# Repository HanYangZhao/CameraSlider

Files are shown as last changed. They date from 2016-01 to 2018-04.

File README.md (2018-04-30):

# Smartphone controlled camera slider using 3D Printed parts and Esp8266

This project started with me wanting to take timelapse photos and videos where the camera is sliding on a set of rails. Because my primary application was timelapse photos, I wanted something that was motorized and automated so that I don't have to manually adjust the slider and cause inconsistency the the photos. Additionally, I wanted to be able to control the rig with a smartphone. Commercial products costs over 500$ and none of them are wireless so I thought I'd make something for much cheaper using 3D printed parts and off the shelf components. The final total cost was under 100$. It is still an ongoing project.

# TODO: 

-iOS app

# Test Footage 

## Video

<a href="http://www.youtube.com/watch?feature=player_embedded&v=VQx5hUlplgQ
" target="_blank">IMAGE ALT TEXT HERE</a>

## Timelapse

<a href="http://www.youtube.com/watch?feature=player_embedded&v=VpbRqibYY6U
" target="_blank">IMAGE ALT TEXT HERE</a>

<a href="http://www.youtube.com/watch?feature=player_embedded&v=ssHNjMlmGzI
" target="_blank">IMAGE ALT TEXT HERE</a>

# Photos 

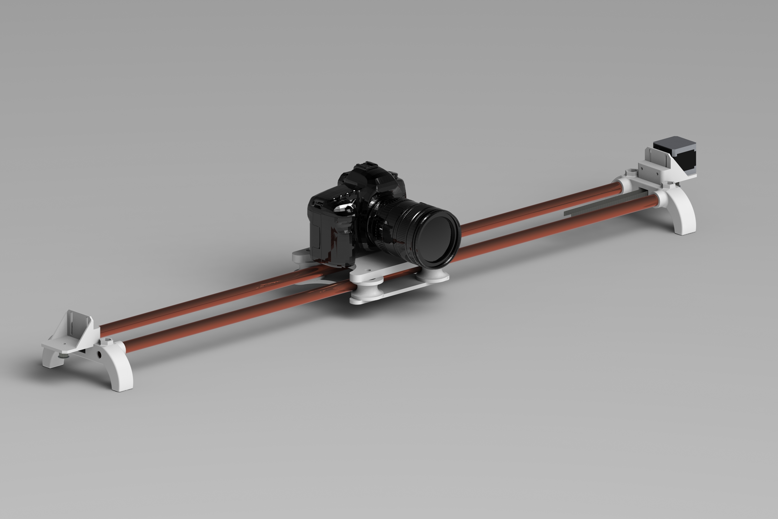
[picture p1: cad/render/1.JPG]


Designed using SolidWorks CAD

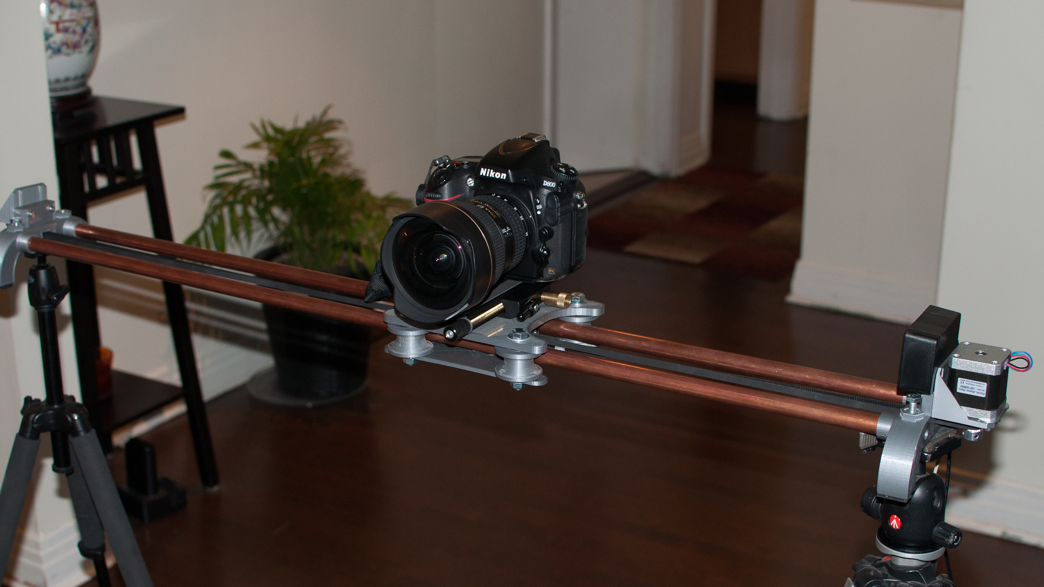
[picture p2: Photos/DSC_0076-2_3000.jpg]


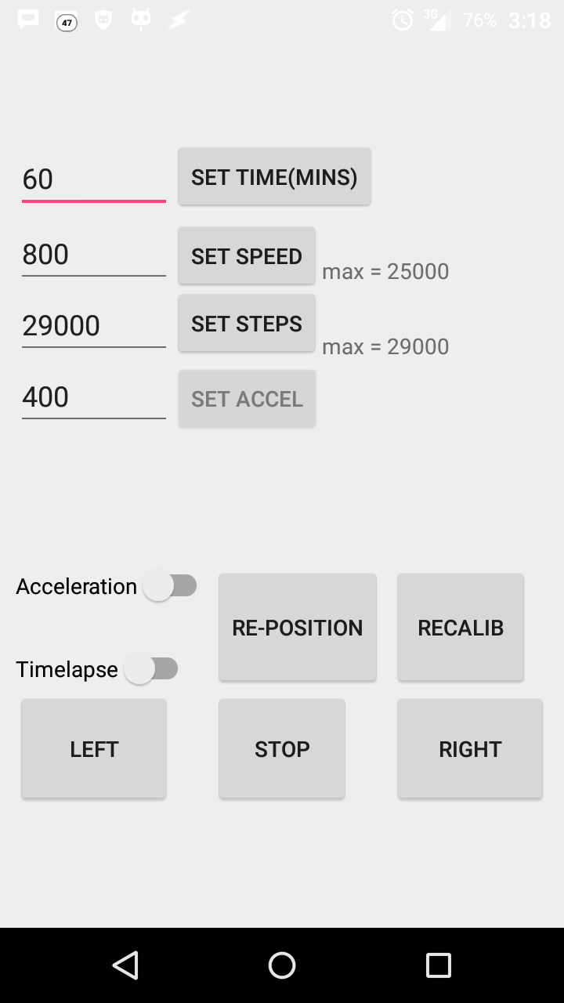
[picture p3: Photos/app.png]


# Materials

2 x  1/2 inch copper tubing as rails. I used a meter for each rail.

8 x 608 bearings for the rollers

NEMA 17 Stepper motor with 2x20 Tooth GT2 gears to drive the plate.

1x ESP8266 Adafruit Huzzah  + FTDI cable

1x A4988 Stepper Motor Driver Carrier, Black Edition

5V power bank as power source with 2 output. 2A min on one the output

4 x 8mm bolts and nuts for the skateboard bearing

4 x 4mm bolts to and nuts attached the stepper motor plate to the chassis

2 x 3mm bolts to attached the stepper motor to the stepper motor plate

2 x 4 mm bolts and nuts to attached the belt to the bottom plate

1 x  mm bolt and nuts + washer to hold the free spinning gear to one of the plates

1 x Small box to put all the electronics.

1 x 470uF Cap

1 x 5V to 12V voltage converter

1 x 1/4 inch or 3/8 inch bolt to attach the camera

2 x 3.5mm power jack

2 x usb cables

# Hardware assembly

Hardware assembly is pretty self-explanatory. You can use the photos in the photo folder to get the idea. The top plate to support the camera includes a hole for 1/4 inch bolts and 3/8 inch bolts. You can either attach you camera directly to the plate or use a micro sliding plate to better control the balance of camera on the plate. This is especially useful for big and heavy camera like the d800.

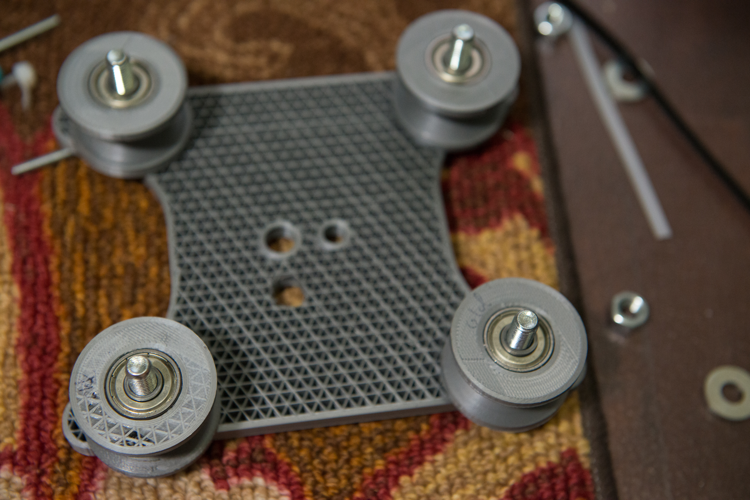
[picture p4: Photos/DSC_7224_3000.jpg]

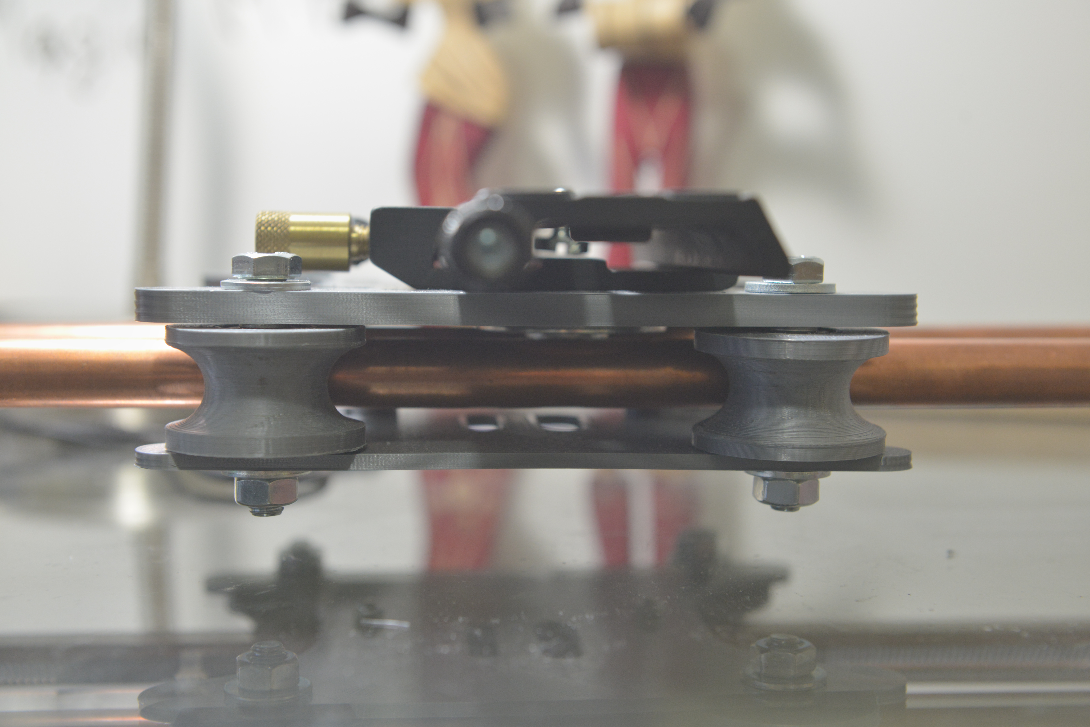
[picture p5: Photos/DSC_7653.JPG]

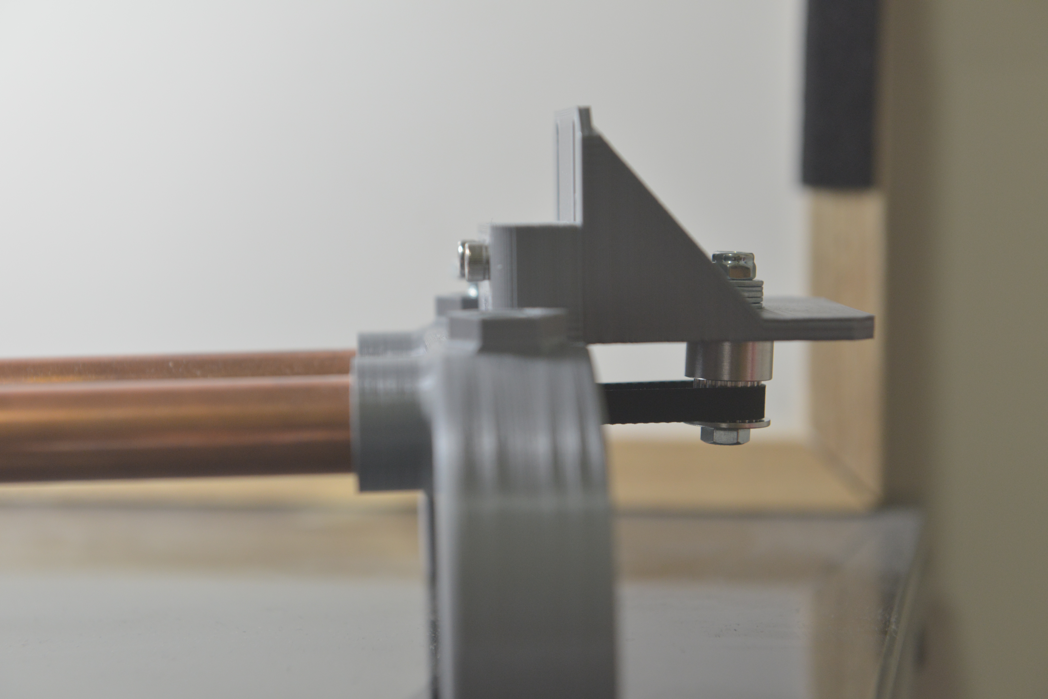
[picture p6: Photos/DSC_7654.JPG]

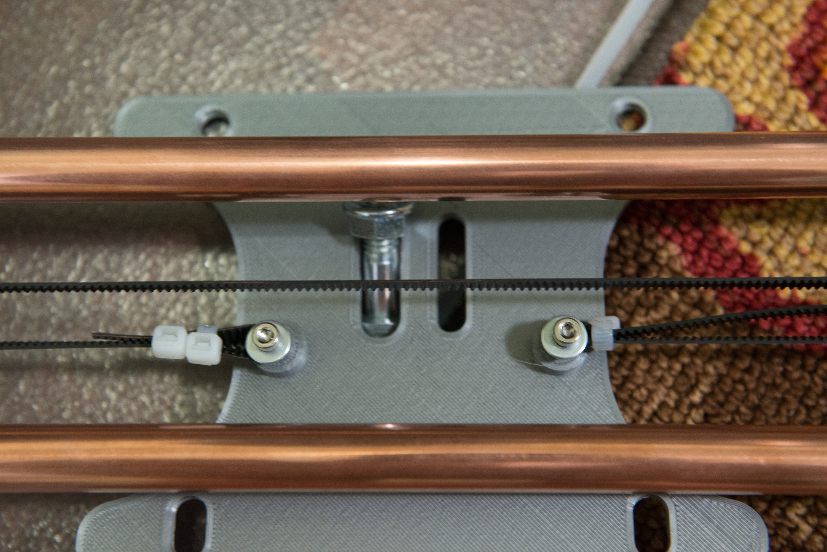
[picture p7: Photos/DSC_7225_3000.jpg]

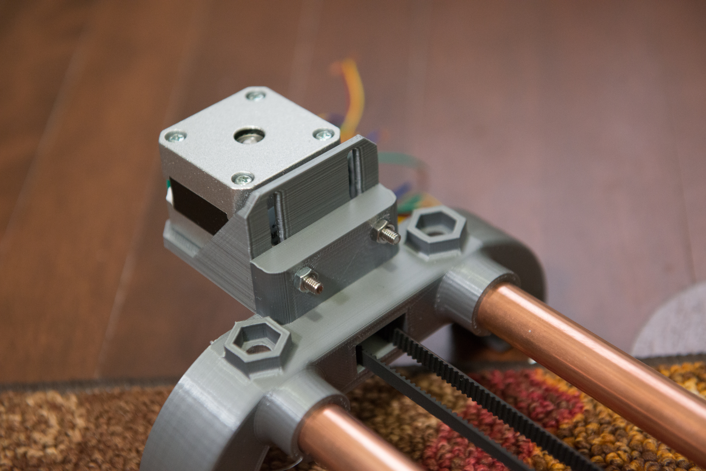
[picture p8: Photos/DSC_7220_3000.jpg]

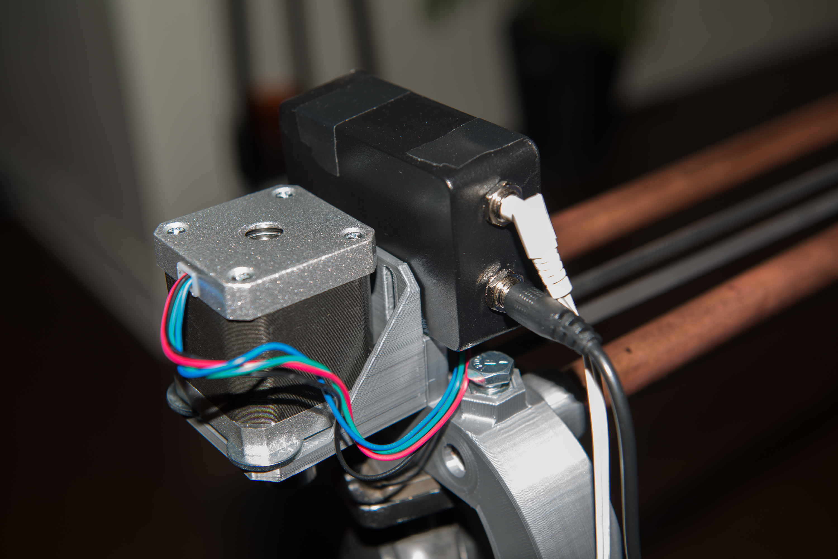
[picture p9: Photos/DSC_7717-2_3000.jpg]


To connect the electronics. Use [this guide] (https://www.pololu.com/product/2128)





The MCU will be the esp8266 and the 8-35V input will be the output of the 5 to 12V converter (the 2A one)

The logic power supply will be from 2nd output of the power bank.

# Software

There are 2 folders. One for the esp8266 code and one for the Android app. The esp8266 acts as a WiFi AP. The Android phone connects to the Esp8266 and controls is by sending html messages.

You'll need AccelStepper library for the stepper motor (http://www.airspayce.com/mikem/arduino/AccelStepper)

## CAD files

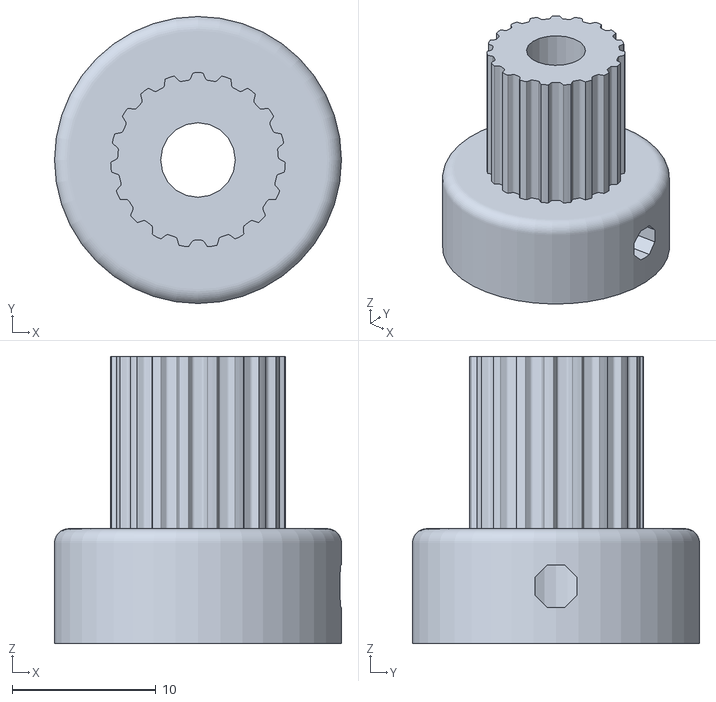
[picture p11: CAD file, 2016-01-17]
cad/solidworks/Parametric_pulley_-_lots_of_tooth_profiles/40DP-19T-OD12.17.stl
20.0 x 20.0 x 20.0

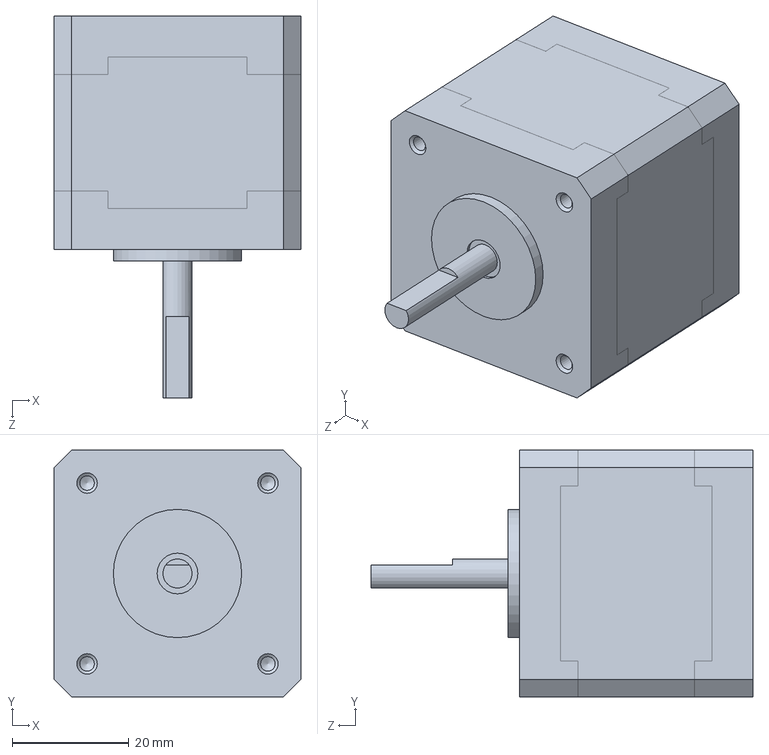
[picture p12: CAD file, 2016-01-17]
cad/solidworks/stepper.SLDPRT
42.3 x 42.3 x 65.5 mm

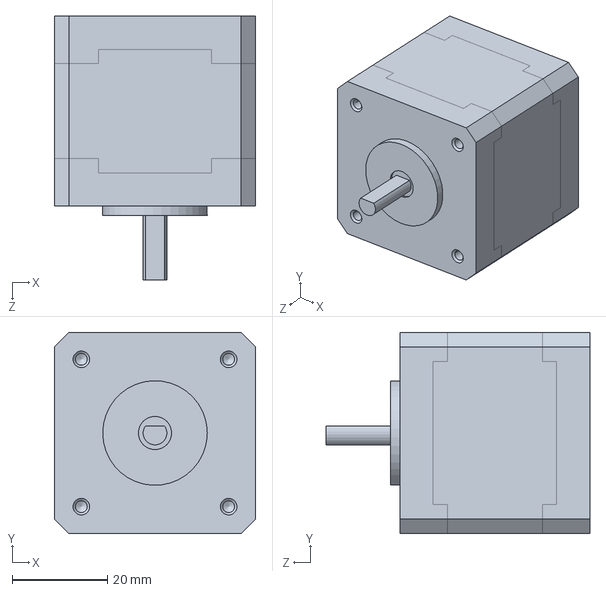
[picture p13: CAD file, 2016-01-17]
cad/solidworks/0,47.SLDPRT
42.3 x 42.3 x 55.5 mm

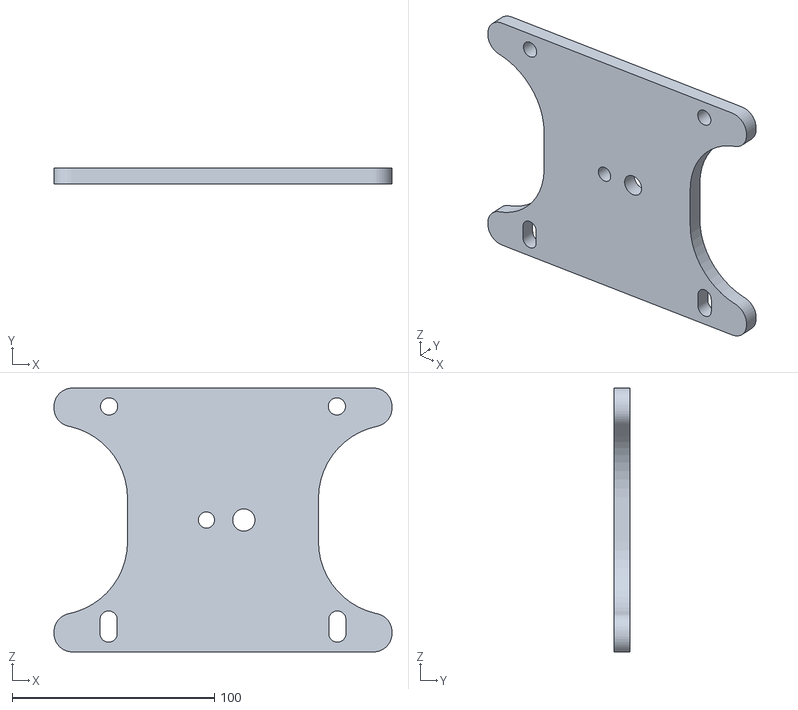
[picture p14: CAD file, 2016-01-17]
cad/stl/top_plate.STL
167.0 x 8.00 x 130.4

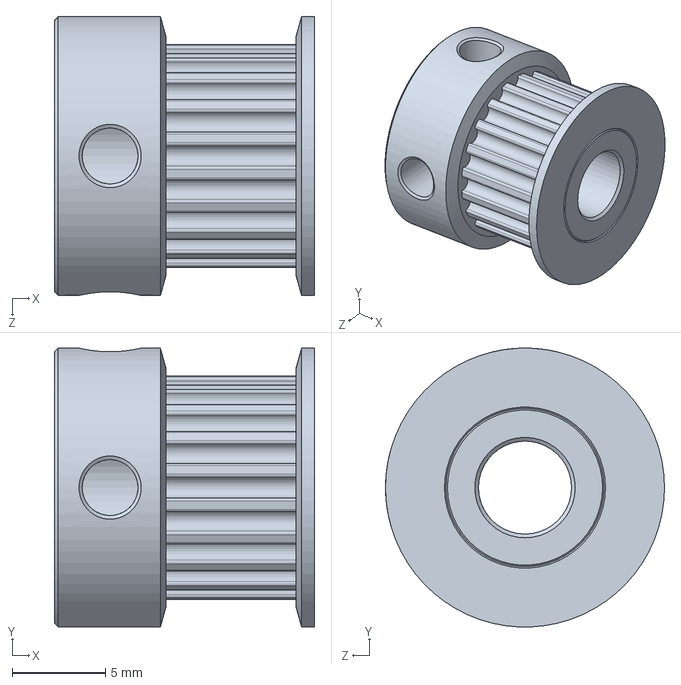
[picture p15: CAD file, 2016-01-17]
cad/solidworks/GT2_20tooth.SLDPRT
14.0 x 15.0 x 15.0 mm

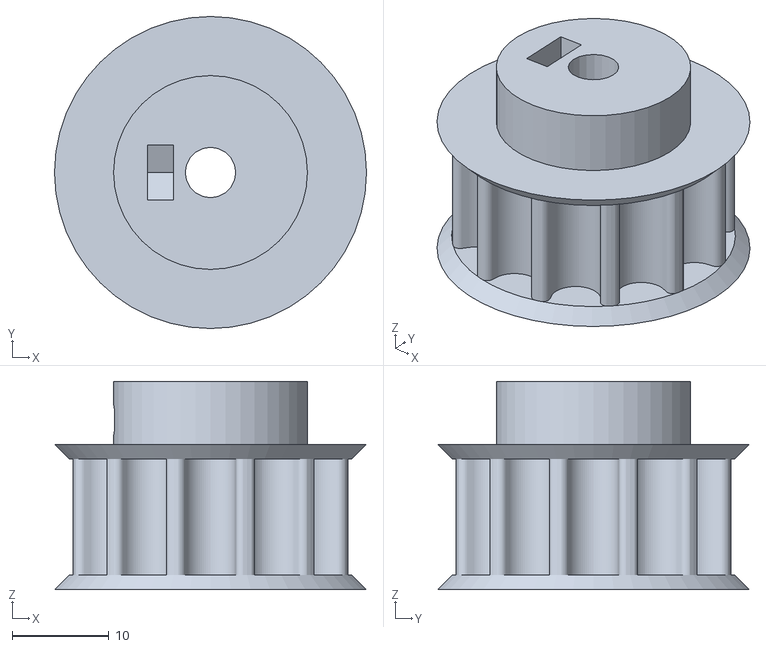
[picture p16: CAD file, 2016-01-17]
cad/solidworks/Parametric_pulley_-_lots_of_tooth_profiles/HTD_8mm-12T-OD29.18.stl
32.2 x 32.2 x 21.5

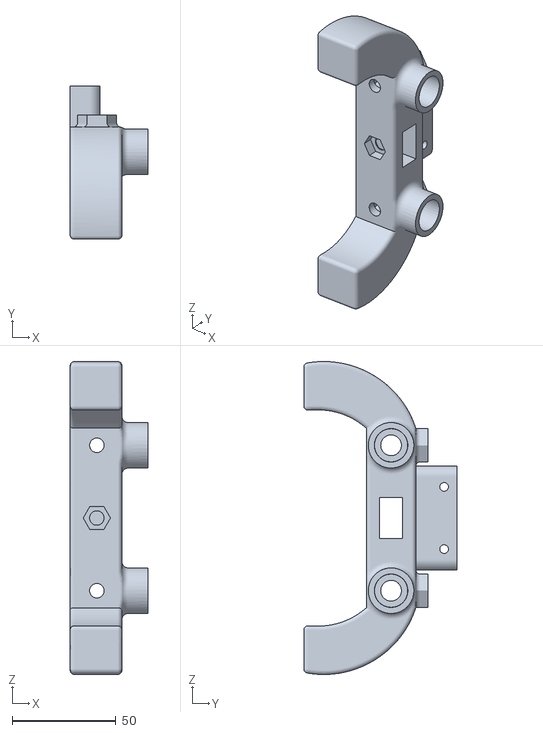
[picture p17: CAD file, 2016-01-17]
cad/stl/SIDE.STL
37.5 x 74.1 x 151.1

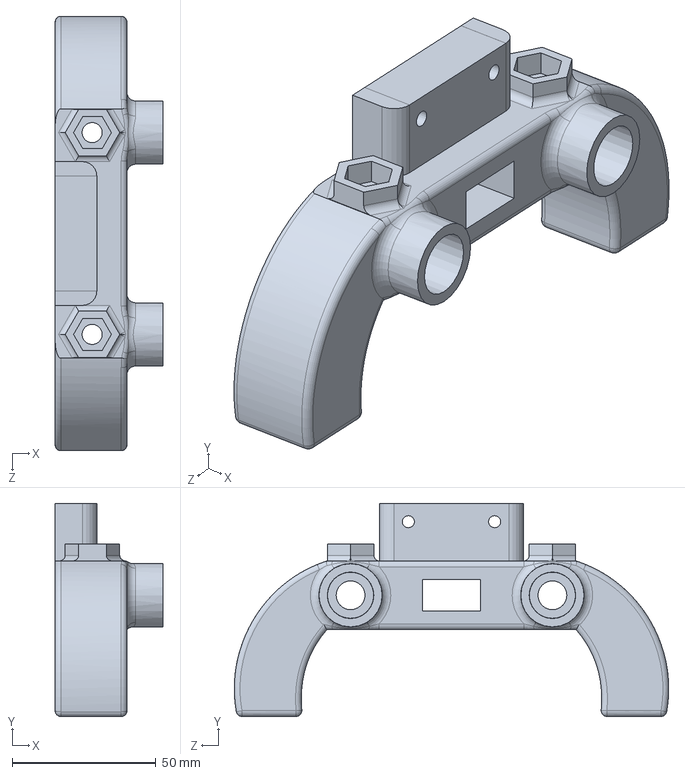
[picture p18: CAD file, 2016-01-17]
cad/solidworks/side_v3.SLDPRT
37.5 x 74.1 x 151.1 mm

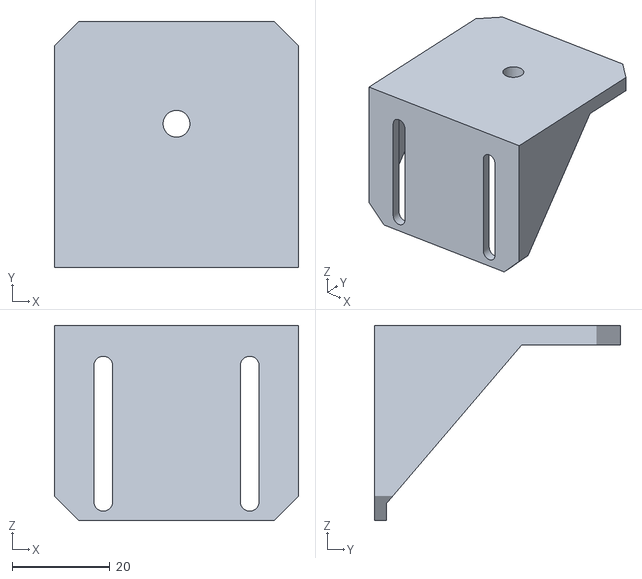
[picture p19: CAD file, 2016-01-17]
cad/stl/idler_mount.STL
50.0 x 50.5 x 40.0

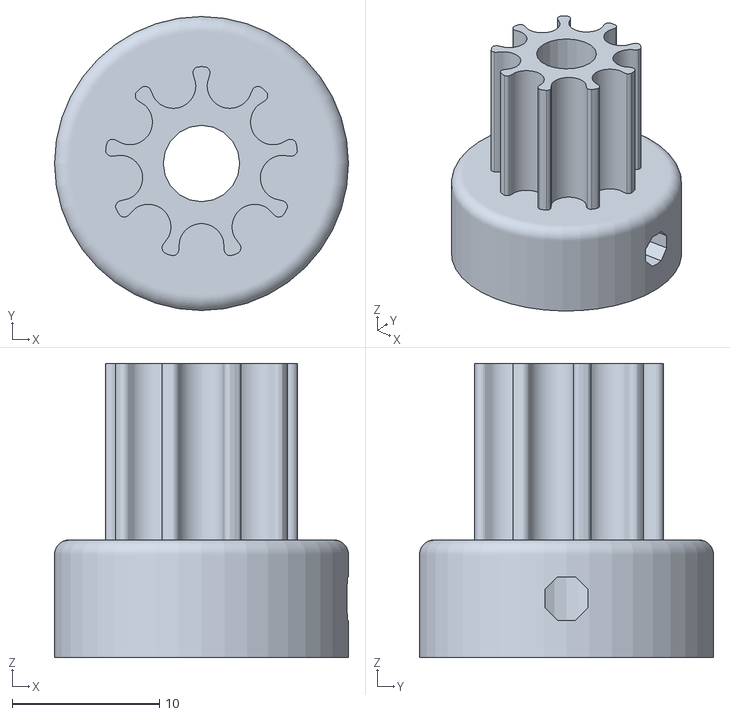
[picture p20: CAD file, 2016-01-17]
cad/solidworks/Parametric_pulley_-_lots_of_tooth_profiles/HTD_5mm-9T-OD13.18.stl
20.0 x 20.0 x 20.0

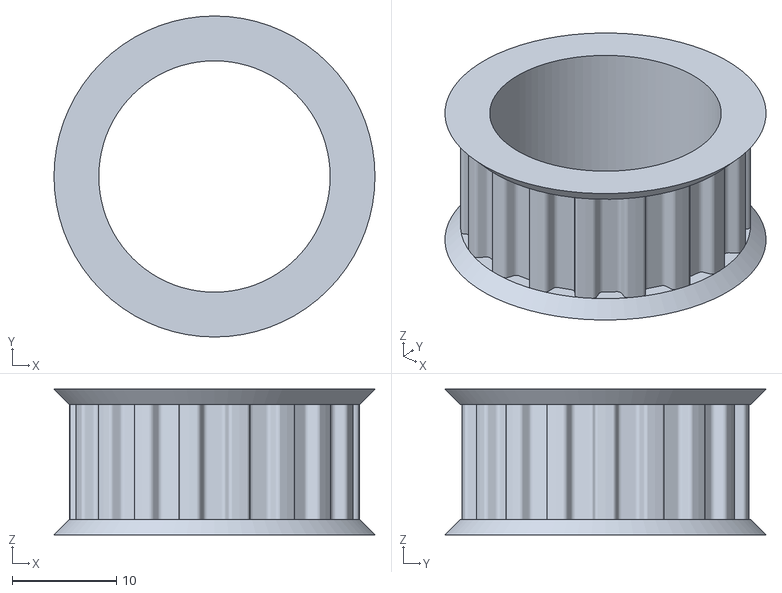
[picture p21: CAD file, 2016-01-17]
cad/solidworks/Parametric_pulley_-_lots_of_tooth_profiles/T5-18T-608-idler.stl
30.8 x 30.8 x 14.0

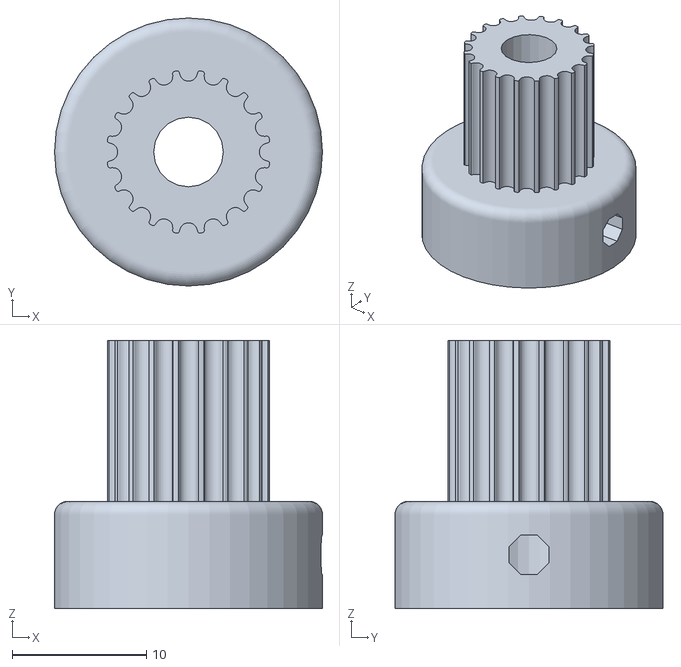
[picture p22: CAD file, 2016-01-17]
cad/solidworks/Parametric_pulley_-_lots_of_tooth_profiles/GT2_2mm-20T-OD12.22.stl
20.0 x 20.0 x 20.0

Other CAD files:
cad/solidworks/Parametric_pulley_-_lots_of_tooth_profiles/T2.5-16T-OD12.20.stl
cad/solidworks/Parametric_pulley_-_lots_of_tooth_profiles/GT2_3mm-13T-OD11.65.stl
cad/solidworks/Parametric_pulley_-_lots_of_tooth_profiles/AT5-8T-OD11.88.stl
cad/solidworks/Parametric_pulley_-_lots_of_tooth_profiles/XL-8T-OD12.42.stl
cad/solidworks/Parametric_pulley_-_lots_of_tooth_profiles/T5-8T-OD11.88.stl
cad/solidworks/Parametric_pulley_-_lots_of_tooth_profiles/Pulley_T-MXL-XL-HTD-GT2_N-tooth.scad
cad/solidworks/Parametric_pulley_-_lots_of_tooth_profiles/GT2_5mm-8T-OD11.58.stl
cad/solidworks/Parametric_pulley_-_lots_of_tooth_profiles/H-10T-OD29.55.stl
cad/solidworks/Parametric_pulley_-_lots_of_tooth_profiles/HTD_3mm-13T-OD11.65.stl
cad/solidworks/Parametric_pulley_-_lots_of_tooth_profiles/MXL-20T-OD12.42.stl
cad/solidworks/Parametric_pulley_-_lots_of_tooth_profiles/T10-10T-OD29.97.stl

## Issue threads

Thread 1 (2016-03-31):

Great project!

msurguy, 2016-03-31:
This is a very cool project!

Could this technically be done with ESP-01 that has only a few outputs?

Also, it seems that the Android app is only sending GET requests which could be doable with a web app and further PhoneGap shell around it to make it cross platform, is that a possibility?

HanYangZhao, 2016-03-31:
Hi,

It should be possible since the communication between the esp and the stepper driver needs 2 pins, which the esp 01 has. It will be slightly annoying as you'll need to ground the pin 0 everytime you upload a new code to the esp.

Web-app is should also be possible. Like you mentioned it is currently only a 1 way communication, but eventually I would like the esp to send back its status back to the app. Unfortunately I havent got anytime to work on it right now.

Thanks!

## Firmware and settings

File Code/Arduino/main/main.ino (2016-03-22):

/* Create a WiFi access point and provide a web server on it. */

#include <ESP8266WiFi.h>
#include <WiFiClient.h> 
#include <ESP8266WebServer.h>
#include <AccelStepper.h>
#include "Timer.h";

AccelStepper stepper(1,5,4);
//pin 5 step, pin 4 dir

/* Set these to your desired credentials. */
const char *ssid = "CameraSlider";
const char *password = "thereisnospoon";

float stepper_speed = 10000;
int max_stepper_speed = 100000;
int stepper_accel = 1000;
int timelapse_mins = 60;
long init_pos = 0;
long current_pos = 0;
long steps = 29000 * 4;
bool accel_enabled = false;
bool isStop = false;
int MS1 = 13;
int MS2 = 12;
int MS3 = 14;

String s = "HTTP/1.1 200 OK\r\nContent-Type: text/html\r\n\r\n<!DOCTYPE HTML>\r\n<html>\r\n</html>\n" ;

WiFiServer server(80);

/* Just a little test message.  Go to http://192.168.4.1 in a web browser
 * connected to this access point to see it.
 */

 void setup() {
   pinMode(MS1, OUTPUT);
   pinMode(MS2, OUTPUT);
   pinMode(MS3, OUTPUT);
   //Microstepping is set to 1/16
   digitalWrite(MS1, HIGH);
   digitalWrite(MS2, HIGH);
   digitalWrite(MS3, HIGH);
   delay(1000);
   Serial.begin(115200);
   Serial.println();
   Serial.print("Configuring access point...");
  /* You can remove the password parameter if you want the AP to be open. */
   WiFi.softAP(ssid, password);

   IPAddress myIP = WiFi.softAPIP();
   Serial.print("AP IP address: ");
   Serial.println(myIP);
   server.begin();
   Serial.println("server started");
   stepper.setMaxSpeed(max_stepper_speed);
   stepper.setCurrentPosition(0);
   Serial.println("current_position");
   Serial.println(stepper.currentPosition());
 }
 void moveSlider(String direction){ 
  isStop = false;
  if (direction.equals("left")){
    Serial.println("moving left");
    //stepper.setSpeed(speed); 
    stepper.move(-steps);
    stepper.setSpeed(-stepper_speed); 
  }      
  else if (direction.equals("right")) {
    long start_pos = stepper.currentPosition();
    Serial.println("moving right");
    stepper.move(steps);
    stepper.setSpeed(stepper_speed);
  }

  else if (direction.equals("reset")){
    Serial.println("reset to 0");
    stepper.move(-stepper.currentPosition()); 
    stepper.setSpeed(-stepper_speed); 
  }
}
void changeSpeed(float mot_speed){
  stepper_speed = mot_speed;
  stepper.setAcceleration(mot_speed/4);
  Serial.println(stepper_speed);
}

void timelapse(String direction){
  float timelapse_speed =  36.0f / (timelapse_mins / 60.0f);
  Serial.println(timelapse_speed);
  if (timelapse_speed > max_stepper_speed)
    timelapse_speed = max_stepper_speed;

  isStop = false;
  
  if (direction.equals("left")){
     stepper.move(steps);
     stepper.setSpeed(timelapse_speed);     
  }

  else if (direction.equals("right")){
    stepper.move(-steps);
    stepper.setSpeed(-timelapse_speed);
  }
}

void processGetRequest(String url){
  char * req = strdup(url.c_str());
  float rev_speed = 0.0f;
  int rev_data = 0;
  strtok(req, "?");
  String name = strtok(NULL, "=");
  if (name.equals("speed"))
    rev_speed = atof(strtok(NULL , "="));
  else {
     rev_data = atoi(strtok(NULL , "="));
  }
  
  Serial.println(name);
  if (name.equals("left")){
    moveSlider("left");
  }
  else if (name.equals("right")){
    moveSlider("right");
  }
  else if (name.equals("speed"))
    changeSpeed(rev_speed);
    
  else if (name.equals("stop")){
    Serial.println("stopping");
    isStop = true;
  }
  else if (name.equals("reset_pos")){
    moveSlider("reset");
    isStop = false;
  }

  else if (name.equals("steps")){
    steps = rev_data;
  }
  else if (name.equals("recalibrate")){
    stepper.setCurrentPosition(0);
    Serial.println(stepper.currentPosition());
  }
  else if (name.equals("timelapse_right")){
    timelapse("right");
  }
  else if (name.equals("timelapse_left")){
    timelapse("left");
  }
  else if (name.equals("mins")){
    timelapse_mins = rev_data;
  }

  else if (name.equals("accel_enabled")){
    accel_enabled = rev_data;
  }

  else if (name.equals("set_accel")){
    stepper.setAcceleration(rev_data);
  }
}
void loop() {
  // Check if a client has connected
  if (isStop){
    stepper.stop();
    //Serial.println("stopped");
  }
  else if (!isStop && stepper.distanceToGo() != 0){
    if (!accel_enabled)
      stepper.runSpeed();
    else if (accel_enabled)
      stepper.run();
    Serial.println(stepper.currentPosition());
  }

  
  WiFiClient client = server.available();
  if (!client) {
   return;
 }
    //Wait until the client sends some data
 Serial.println("new client");
 while (!client.available()){
  delay(1);
}
  // Read the first line of the request   
  processGetRequest(client.readStringUntil('\r'));
  client.print(s);
  client.stop();
  
}

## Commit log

2016-01-17 upload cad/photos
    [0,47.SLDPRT, 40DP-19T-OD12.17.stl, AT5-8T-OD11.88.stl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]
2016-03-12 fixed arduino code , added stop button in app
    [main.ino]
2016-03-14 fixed timelapse , added recalibration button
    [main.ino]
2016-03-19 reversed left and right direction, new photo
    [main.ino]
2016-03-21 fixed timelapse formula , updated gradle
    [main.ino]
